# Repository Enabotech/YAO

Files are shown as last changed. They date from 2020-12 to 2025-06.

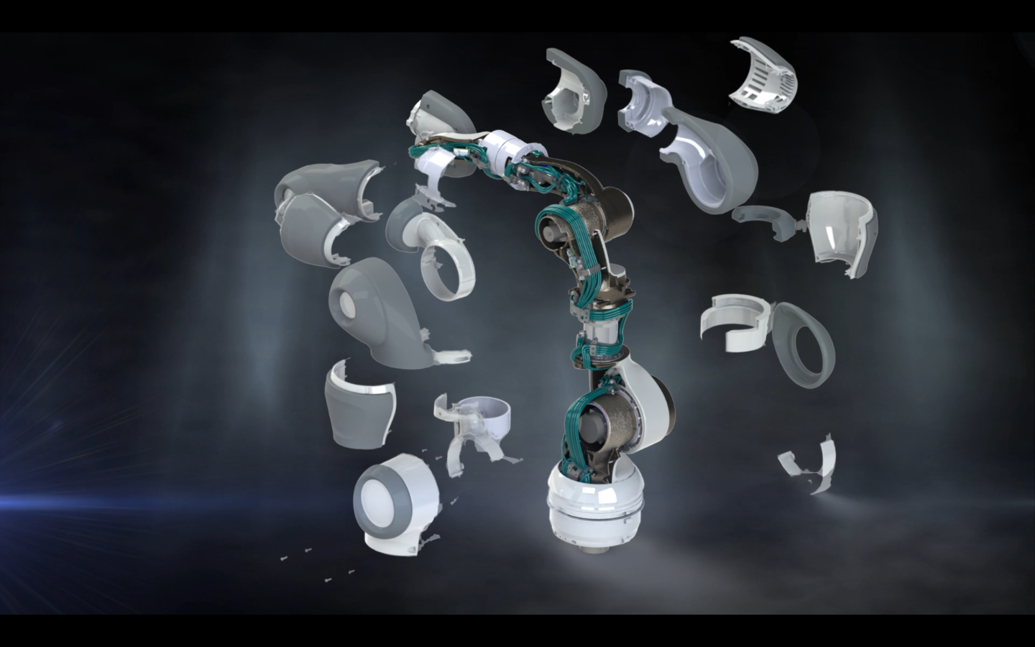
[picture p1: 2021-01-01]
docs/reference/abb/结构图.png

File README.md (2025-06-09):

# YAO
https://github.com/Enabotech/YAO/assets/8104370/9be1e858-5e8b-4420-9542-9bed2b7c62a3

enabotech@126.com

## 电气
### 电机及驱动
* 东方减速步进电机套件。可根据实际需求自行选择合适的电机及驱动方案。
### 运动控制器
* Galil DMC-2183/DMC-4080。可根据实际需求自行选择合适的控制器方案。
### 主控单元
* 基于Ubuntu + ROS Kinetic的PC系统。
## 机械
* 已完成设计及结构验证。主要参考ABB IRB 14000机械臂自行设计。
## 软件
* 完成基于ROS的MOVEIT+GAZEBO仿真系统搭建。
* 初步完成系统框架程序。欢迎PR。
## 逆运动学
| 参数 | 解析解 |
|---|---|
| $\theta_1$ | $$\arctan2(p_y, p_x) - \arcsin{\frac{a_1}{\sqrt{p_x^2 + p_y^2}}}$$ |
| $\theta_2$ | $$\arctan2\left( p_z - d_1, \sqrt{p_x^2 + p_y^2} - a_1 \right) - \arctan2(a_3\sin{\theta_3}, a_2 + a_3\cos{\theta_3})$$ |
| $\theta_3$ | $$\pm \arccos{\frac{L^2 - a_2^2 - a_3^2}{2a_2a_3}}\quad(\text{±号对应肘部"up/down"两种构型})$$ |
| $\theta_4$ | $$\phi - (\theta_2 + \theta_3)$$ |
| $\theta_5$ | $$\arctan2 \left(r_{32}, r_{31}\right)$$ |
| $\theta_6$ | $$\arctan2 \left( \sqrt{r_{11}^2 + r_{21}^2}, r_{33} \right)\quad(\text{为零时退化为万向节锁})$$ |
| $\theta_7$ | $$\arctan2 \left( r_{23}, -r_{13} \right)$$ |
| $\mathbf{p}_{end}$ | $$[p_x, p_y, p_z]^T$$ |
| $L$ | $$\sqrt{(p_z - d_1)^2 + \left( \sqrt{{p_{x}^2 + p_{y}^2}} - a_1 \right)^2}$$ |
| $\phi$ | $$\arg\min \sum_{i=1}^7 \left(\theta_i - \theta_{i,home}\right)^2 \quad (\text{最小能量准则})$$ |
## 图纸
enabot_yao_prj_spec
t
q
w

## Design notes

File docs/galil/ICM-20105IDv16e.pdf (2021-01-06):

ICM-20105ID

## ICM-20105D

ICM-20105D 是为 DMC-21x3 系列运动控制卡配套设计的信号接口板。 ICM-20105D 直 接通过 DIN96 插接在 DMC-21x3 控制卡上，并可通过螺钉锁紧。 ICM-20105D 接口内各引 脚定义与 GALIL 公司的 ICM-20105 基本一致（为方便用户接线与设置， 有个别引脚进行 了调整 ）。

ICM-20105D 上，用户接口为四个运动控制 -反馈接口、一个 I/O 信号接口和一个辅助编 码器接口。

2010 09 | 1 | KIKD

一、运动控制 -反馈接口

DB15 规格的 15 针插座，分别标注为 JX、JY、JZ、JW，对应控制卡上 A（E）、B（F）、 C（G）、D（H）各轴信号。四个接口内的引脚定义是一致的。各引脚信号说明如下：

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
ENABLE+

5V

A-

B-

Z-

V-

SIGN / DIR

9

10

11

12

13

14

15

ENABLE-

GND

A+

B+

Z+

COMMAND

PWM / STEP

V+、V-：
须由用户提供的外部电源，用于驱动电机放大器使能（ SERVER-ON ）信号，四个运动 控制-反馈接口以及辅助编码器接口中的 V+、V-使用同一电源， 用户可以通过任一接口提供 此电源。 V+与 V-之间电压不应大于 30VDC

ENABALE+ 、ENABLE- ：
各轴使能输出信号，用于控制电机放大器或驱动器的使能 （SERVER-ON ）。ENABALE+ 、

ENABLE- 分别为信号隔离光耦的集电极（ Collector ）与发射极（ Emitter ），电流必须由

ENABALE+ 流向 ENABLE- 。
默认状态下， GALIL 控制器使能信号输出为高电平时（电机使能 | SH），ENABALE+ 、
ENABLE- 之间闭合导通； 控制器使能信号输出为低电平时（电机关闭 | MO），ENABALE+ 、

ENABLE- 之间隔离。

默认状态
通过调整 UEN 右侧跳线 X、Y、Z、W 的设置，也可改变上述逻辑状态。 GALIL 控制 器使能信号输出为高电平时 （电机使能 SH），ENABALE+ 、ENABLE- 之间隔离； 控制器使 能信号输出为低电平时（电机关闭 MO），ENABALE+ 、ENABLE- 之间闭合导通。

调整方式，参考板上跳线下的标注。

2010 09 | 2 | KIKD

5V、GND：
DMC-21X3 控制器的 5V 电源，可用于反馈编码器的电源， 也可用于电机运动控制信号 的参考电位。

A+、A-、B+、B-、Z+、Z-：
各轴主编码器反馈信号，直接连至 GALIL 控制器。接收 RS422 或 TTL 信号。

COMMAND ：
各轴+/-10V 电压指令信号，用于控制电机驱动器或放大器。此信号通常用于速度或扭 矩（电流）指令信号。此信号直接连自 GALIL 控制器，以 GND 为参考电位。该信号所能 够提供的电流，请参照 GALIL 控制器手册。

PWM / STEP 、SIGN / DIR ：
各轴的脉冲、方向信号，用于控制电机驱动器或放大器。 此信号通常用于位置指令信号。 此信号直接连自 GALIL 控制器，为 5V TTL 信号。该信号所能够提供的电流， 请参照 GALIL 控制器手册。

用户可以参照附录中的连接举例来按照自己的需求设计此接口与驱动器之间的具体连 接方式，或将驱动器本身的接线说明提供给我们， 由我们协助您实现 ICM-20105D 与您所选 用的驱动器（放大器）的具体连接方式。

二、I/O 信号接口

DB37 规格的 37 孔插座，标注为 JIO，用于连接 I/O 信号。信号与 GALIL 控制卡之间 采用光耦进行了电气隔离。接口中各引脚定义如下：

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
2010 09

INPUT COMMON

INPUT 2

INPUT 4

INPUT 6

INPUT 8

OUTPUT COMMON

OUTPUT 2

OUTPUT 4

OUTPUT 6

3

20 | INPUT 1
21 | INPUT 3
22 | INPUT 5
23 | INPUT 7
24 | ABORT
25 | OUTPUT 1
26 | OUTPUT 3
27 | OUTPUT 5
28 | OUTPUT 7

KIKD

10 | OUTPUT 8
11 | LIMIT SWITCH COMMON
12 | REVERSE LIMIT X
13 | FORWARD LIMIT Y
14 | HOME Y
15 | REVERSE LIMIT Z
16 | FORWARD LIMIT W
17 | HOME W
18 | 5V
19 | GND
29 | READY
30 | FORWARD LIMIT X
31 | HOME X
32 | REVERSE LIMIT Y
33 | FORWARD LIMIT Z
34 | HOME Z
35 | REVERSE LIMIT W
36 | 5V
37 | GND

INPUT COMMON 、INPUT1 —INPUT8 、ABORT：

通用输入以及急停输入信号，对应 GALIL 控制器上的通用输入 IN1（9）、IN2（10）、

IN3（11）、IN3（12）、IN5（13）、IN6（14）、IN7（15）、IN8（16）与急停输入（*1。INPUT COMMOM 为以上信号的内部公共端， 当输入信号引脚与公共端之间有电流时， 为有效输入 （对应 GALIL 控制器输入信号为低）；无电流时，为无效输入，（对应 GALIL 控制器输入信 号为高）。由于使用的光偶器件为双向输入，所以， INPUT COMMOM 既可以接高电平，也 可以接低电平。

ICM-20105ID 输入信号按照 24VDC 规格设计，外部电压 12VDC—30VDC （ 电 流 约 2—6mA）有效。外部电压 0—5VDC（电流小于 1mA）为无效输入。（*2
在 GALIL 的控制器上，通用输入的 1、2、3、4 也可作为位置锁存信号使用。光耦的隔 离处理在增加了应用便利的同时， 也会造成信号相应的延迟，如用户需要比较高的响应速度， 可参照附录中的方式接入位置锁存信号。

OUTPUT COMMON 、OUT1—OUT8、READY ：

通用输出及控制就绪 （异常报警）输出信号，对应 GALIL 控制器的 OUT1（9）、OUT2

（10）、OUT3（11）、OUT4（12）、OUT5（13）、OUT6（14）、OUT7（15）、OUT8（16） 与 ERROR 信号输出。OUTPUT COMMON 为以上输出信号的负公共端。默认状态下，当控 制器输出信号为高电平时， JIO 内相应输出脚与 OUTPUT COMMON 之间导通；当控制器输 出信号为低电平时， JIO 内相应输出脚与 OUTPUT COMMON 之间开路。（*3 输出隔离采用达林顿（ DARLINGTON ）输出光耦元件，开路状态下，最大开路电压为

30V。导通状态下，每路输出信号可通过的最大电流为 | 100mA ，信号输出点与 OUTPUT
2010 09 | 4 | KIKD

COMMON 之间会有约 0.6V 的导通压降，可兼容 TTL 或 HTL 规格。

LIMIT SWITCH COMMON 、FORWARD LIMIT X 、REVERSE LIMIT X 、HOME X 、 FORWARD LIMIT Y 、REVERSE LIMIT Y 、HOME Y、FORWARD LIMIT Z 、REVERSE LIMIT Z、HOME Z 、FORWARD LIMIT W 、REVERSE LIMIT W 、HOME W

各轴的前后极限及原点输入信号， LIMIT SWITCH COMMON 为各轴的前后极限及原点 输入信号的内部公共端， 当输入信号引脚与公共端之间有电流时， 为有效输入（对应 GALIL 控制器输入信号为低）；无电流时，为无效输入，（对应 GALIL 控制器输入信号为高）。由于 使用的光偶器件为双向输入，所以， LIMIT SWITCH COMMOM 既可以接高电平，也可以 接低电平。

ICM-20105ID 输入信号按照 24VDC 规格设计，外部电压 12VDC—30VDC （ 电 流 约 2—6mA）有效。外部电压 0—5VDC（电流小于 1mA）为无效输入。（*2

5V、GND：
GALIL 控制器电源信号，不推荐使用。

三、辅助编码器接口
DB25 规格的 25 孔插座，接口内各引脚定义如下

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
AB- W

AA- W

AB- Z

AA- Z

AB- Y

AA- Y

AB- X

AA- X

NC

5V

V+

COMPARE

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
AB+ W

AA+ W

AB+ Z

AA+ Z

AB+ Y

AA+ Y

AB+ X

AA+ X

NC

GND

V-

AB-W、AB+W、AA-W、AA+W、AB-Z、AB+Z、AA-Z、AA+Z、AB-Y、AB+Y、AA-Y、 AA+Y、AB-X、AB+X、AA-X、AA+X：
各轴的辅助编码器输入信号，也可作为通用输入信号使用（详见《 DMC-21x3 手册》）。 信号直连至 GALIL 运动控制器，可接受 RS422 或 TTL 信号。
2010 09 | 5 | KIKD

5V、GND：
GALIL 控制器电源信号，不推荐使用。

V+、V-：
须由用户提供的外部直流电源，与 JX、JY、JZ、JW 接口中 V+、V-为同一电源，可用 于驱动电机放大器使能（ SERVER-ON ）信号， V+与 V-之间电压不应大于 30VDC

COMPARE ：
位置比较输出信号，直连至 GALIL 运动控制器，为 TTL 输出。
（1.6d 及之前的版本，此引脚未连接。用户如须使用此信号，请参见附录中的说明）

注释：
（*1：默认状态下，急停输入为常开（ normal open ）输入。如用户处于安全考虑，需要采用 常闭（normal close）输入形式，可通过跳线进行调整。该跳线标注为 JPAB。下图为 JPAB 的默认设置状态。
将跳线设置为 | 状态，急停信号为常闭（ normal close）输入。此时，如急
停输入未接线，则 GALIL 控制器不能控制电机运动。

（*2：JIO 接口中，所有输入信号默认状态均为 24VDC 规格，使用 5.6K 阻值的限流电阻。 外部电压 12VDC—30VDC （电流约 2—6mA）为有效输入；外部电压 0—5VDC（电流小 于 1mA）为无效输入。

### 如用户采用较低电压规格的信号，则须在 RPX、RPY、RPZ、RPW、RPIN1A 、RPIN2A

插入 B 型电阻排，通过并联的方式降低信号输入电路中的限流电阻。电阻排的插座在

### ICM-20105ID 的背面。

如输入信号为 TTL 规格，建议采用阻值为 1.0K—1.5K 电阻排；如输入为 12V 规格，建 议采用 10K——15K 阻值的电阻排。

（*3：通用输出与 READY 信号输出的逻辑状态和极性调整
调整 JIO 中的输出信号，涉及到 JPO 跳线以及所有的输出光耦。 JPO 跳线 ICM-20105ID 的左边，JIO 接口下面的位置。光耦元件是接口 JIO 的下方（背面）的双列直插的 IC 元件。 默认状态下， JIO 中的输出信号为为漏型输出（公共端极性为负） ，此时 JPO 下面两针 脚短路，上面针脚悬空； 光耦器件靠右排列， 器件插座左边两个插脚位置悬空（如下图所示 意）。
2010 09 | 6 | KIKD

如特殊情况下， 用户需要采用源型输出 （公共端极性为正），需要将输出光耦元件平移， 靠左排列，使插座右侧的两个位置空闲，同时将 JPO 跳线的上面两个接点短接，下面一个 接脚悬空。

这时，输出电路结构如下图。控制器输出为低电平时， JIO 中相应接点与 OUTPUT

COMMON 导通，OUTPUT COMMON 为正公共端。

2010 09 | 7 | KIKD

附录
1、 RESET 信号的连接
RESET 信号在默认状态下不连接到用户接口中， 如必须使用该信号，可将其接在 JAUX 的 1 或 14 脚。在 JAUX 接口的左下角，预留了 3 个接点的跳线位置（未焊接），左边接点 为 JAUX 的 14 脚（标注为 14），中间接点为 RESERT 信号（标注为 RST），右边接点 JAUX 接口的第 1 脚（标注为 1）。短接相应接点，就可以将 RESET 信号连接到 JAUX 接口的第 1 脚或第 14 脚。RESET 信号本身为 TTL 兼容信号，在接口板上未做任何隔离、保护处理。

2、 位置比较输出信号的连接

在 1.6d 及之前的版本中，位置比较输出信号在默认状态下不连接到输出接口上，如必 须使用该信号，可将其接在 JAUX 的 13 脚。在 JX 与 JY 两个接口之间，略偏上的位置上， 预留了 2 个接点的跳线位置（未焊接），左边接点为 JAUX 的 13 脚（标注为 13），右边接点 为位置比较输出信号 （标注为 CO）。短接这两个接点， 就可以将位置比较输出信号从 JAUX 接口的第 13 脚接出。位置比较输出信号本身为 TTL 信号，在接口板上未做任何隔离、保护 处理。
（在 1.6e 的版本中，取消此跳线，位置比较输出信号已经连接到 JAUX 的 13 脚）

3、 高速位置锁存信号的连接
各轴位置锁存信号与通用输入信号为同一信号。 由于接口板对通用输入信号进行了隔离 处理，会造成一定的信号延迟。 如必须避免这一信号延迟 （例如触发锁存的信号脉冲比较窄， 或确实需要较高的响应速度），可以跨过隔离处理元件，将输入信号从 JAUX 接口直接连到

DMC-21x3 控制器上。
在 JX 与 JY 两个接口之间，略偏上的位置，分别有标注为 14、LX 与 1、LY 的预留跳 线位置（未焊接）。LX 为 X 轴锁存信号（通用输入 1）；LY 为 Y 轴锁存信号（通用输入 2）；

1 为 JAUX 的第 1 脚；14 为 JAUX 的第 14 脚；短接相应接点，就可以将 X、Y 轴的锁存信 号通过 JAUX 接口的第 1 脚、第 14 脚接入。

2010 09 | 8 | KIKD

如果选择了从 JAUX 的 1 脚或 14 脚接入 RESET 信号，则该脚不可同时用于位置锁存 信号的连接。
在 JAUX 接口的右侧， 分别有标注为 LW、10、23、LZ 的预留跳线位置（未焊接）。LW 为 W 轴锁存信号（通用输入 4）；LZ 为 Z 轴锁存信号（通用输入 3）；10 为 JAUX 的第 10 脚；23 为 JAUX 的第 23 脚；短接相应接点，就可以将 Z、W 轴的锁存信号通过 JAUX 接口 的第 10 脚、第 23 脚接入。

4、 版本记录

1.6e

1.6d

1.6c

1.5b

1.4a

1.3a

取消位置比较输出信号跳线，将信号直连至 JAUX 的 13 脚 调整排阻插座的位置，避免空间冲突

调整排阻插座的位置，减少空间冲突
将大部分器件调整到电路板背面，方便用户自行设计控制器外壳 名称由 ICM-20105D 调整为 ICM-20105ID

增加各轴 COMMAND 信号的电压防护电路
将急停设置跳线的标注由 AB 调整为 JPAB

增加 AB 设置跳线
将所有接头外壳通过固定铜柱连接到 GALIL 控制器上。 （DMC-2153 —DMC-2183 的第二接口板下的固定孔本身并未连接至保护地 上，如用户需要，须自行使用导线连接）

最初应用版本
最初试验品

1.2a

1.0a

5、 伺服连接举例
A、 安川 SGDM 系列伺服驱动器的连接

ICM-20105D 连接安川 SGDM 系列伺服驱动器，要为 V+、V- 提供 12—24VDC 电源， 使能设置跳线 X、Y、Z、W 保持默认状态， JX（或 JY、JZ、JW）与驱动器的 CN1 之间如 下表接线：

ICM-20105D — JX
引脚

11

2010 09

SGDM — CN1
引脚

33

信号

A+

9

备注

双绞线

KIKD

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
COMMAND
GND

5V

PWM / STEP

5V

SIGN / DIR

V+

ENABLE+

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
V-REF
SG

PULS+

PULS-

SIGN+

SIGN-

+24VIN

S-ON

位置反馈信号

双绞线
位置反馈信号

双绞线
位置反馈信号

双绞线
速度指令信号

位置指令信号

9、7 ENABALE- 、V-

使能信号
（ICM-20105D 侧 9、7 两引脚短接，不
需要连接至驱动器）

B、松下 MINAS A4 系列伺服驱动器的连接

ICM-20105D 连接松下 MINAS A4 系列伺服驱动器，要为 V+、V- 提供 12—24VDC 电 源，使能设置跳线 X、Y、Z、W 保持默认状态， JX（或 JY、JZ、JW）与驱动器的 CN I/F 之间如下表接线：

ICM-20105D — JX
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
PWM / STEP

5V

SIGN / DIR

COMMAND
GND

V+

ENABLE+

ENABALE- 、
V-

MINAS A4 — CN I/F
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
PULS1

PULS2

SIGN1

SIGN2

SPR
GND

COM+

S-ON

COM-

使能信号
（ICM-20105D 侧 9、7 两引脚短接）

双绞线
速度指令信号

位置指令信号
（MT 参数设置为 2 或 2.5）

备注

双绞线
位置反馈信号

双绞线
位置反馈信号

双绞线
位置反馈信号
2010 09 | 10 | KIKD

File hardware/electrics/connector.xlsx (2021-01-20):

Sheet: vexta signal connector
as signal connector |  |  |  | ar signal connector
Pin | Description | Color | Enabot Wiring | Pin | Description | Color | Enabot Wiring
1 | VCC+5V | brown | 1 | 1
2 | GND | wh-brown | 2 | 2 | GND | wh-brown | 2
3 |  |  |  | 3 | ASG+ | purple | 9
4 | - |  |  | 4 | ASG- | wh-purple | 10
5 | - |  |  | 5 | BSG+ | orange | 7
6 | - |  |  | 6 | BSG- | bl-orange | 8
7 | - |  |  | 7 | TIM1+
8 | - |  |  | 8 | TIM1-
9 | CCW(DIR)+ | green | 3 | 9 | ALARM+ | yellow
10 | CCW(DIR)- | bl-green | 4 | 10 | ALARM- | bl-yellow
11 | CW(PLS)+ | red | 5 | 11 | WNG+
12 | CW(PLS)- | bl-red | 6 | 12 | WNG-
13 |  |  |  | 13 | END+ | gray
14 |  |  |  | 14 | END- | bl-gray
15 |  |  |  | 15 | READY+/AL0+
16 |  |  |  | 16 | READY-/AL0-
17 | BSG2+ | orange | 7 | 17 | TLC+/AL1+
18 | BSG2- | bl-orange | 8 | 18 | TLC‒/AL1‒
19 | ASG2+ | purple | 9 | 19 | TIM2+/AL2+ | blue
20 | ASG2- | wh-purple | 10 | 20 | TIM2-/AL2- | wh-blue
21 | ACL+ | white |  | 21 | GND |  | 2
22 | ACL- | bl-white |  | 22 | IN-COM | brown | 1
23 |  |  |  | 23 | C-ON | black | 12
24 |  |  |  | 24 | CLR/ALM-RST | white
25 | ALARM+ | yellow |  | 25
26 | ALARM- | bl-yellow |  | 26
27 | TIM.2 | blue |  | 27
28 |  |  |  | 28
29 | END+ | gray |  | 29
30 | END- | bl-gray |  | 30
31 | x10 | wh-blue |  | 31 | CW(PLS)+ | red | 5
32 |  |  |  | 32 | CW(PLS)- | bl-red | 6
33 | C.OFF+ | black |  | 33
34 | C.OFF- | wh-black | 12 | 34
35 | - |  |  | 35 | CCW(DIR)+ | green | 3
36 | - |  |  | 36 | CCW(DIR)- | bl-green | 4

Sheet: galil
icm-20105 X/Y/Z axis connector |  |  |  | icm-20105 I/O connector
Pin | Description | Color | Enabot Wiring | Pin | Description | Color | Enabot Wiring
1 | Amp enable common-1/V+ |  | 11 | 1 | Input common
2 | Amp enable |  | 12 | 2 | Input 2
3 | 5 V |  | 1/3/5 | 3 | Input 4
4 | A- |  | 10 | 4 | Input 6
5 | B- |  | 8 | 5 | Input 8
6 | Z- |  |  | 6 | Output supply
7 | NC |  |  | 7 | Output 2
8 | Sign/dir |  | 4 | 8 | Output 4
9 | Amp enable common-2/V- |  |  | 9 | Output 6
10 | Ground |  | 2 | 10 | Output 8
11 | A+ |  | 9 | 11 | Limit switch common | bl-gray | UC
12 | B+ |  | 7 | 12 | Reverse limit X | bl-red | UC
13 | Z+ |  |  | 13 | Forward limit Y | green | UC
14 | Motor command |  |  | 14 | Home Y | gray | UC
15 | PWM/step |  | 6 | 15 | Reverse limit Z | wh-blue | UC
 |  |  |  | 16 | Forward limit W | yellow | UC
 |  |  |  | 17 | Home W | white | UC
 |  |  |  | 18 | 5 V | brown | UC
 |  |  |  | 19 | Ground | black | UC
 |  |  |  | 20 | Input 1
 |  |  |  | 21 | Input 3
 |  |  |  | 22 | Input 5
 |  |  |  | 23 | Input 7
 |  |  |  | 24 | Abort* | wh-black | UC
 |  |  |  | 25 | Output 1
 |  |  |  | 26 | Output 3
 |  |  |  | 27 | Output 5
 |  |  |  | 28 | Output 7
 |  |  |  | 29 | Output return
 |  |  |  | 30 | Forward limit X | red | UC
 |  |  |  | 31 | Home X | purple | UC
 |  |  |  | 32 | Reverse limit Y | bl-green | UC
 |  |  |  | 33 | Forward limit Z | blue | UC
 |  |  |  | 34 | Home Z | orange | UC
 |  |  |  | 35 | Reverse limit W | bl-yellow | UC
 |  |  |  | 36 | 5 V | brown | UC
 |  |  |  | 37 | Ground | black | UC
 |  |  |  |  | *Active low
 |  |  |  |  | UC-Use Color

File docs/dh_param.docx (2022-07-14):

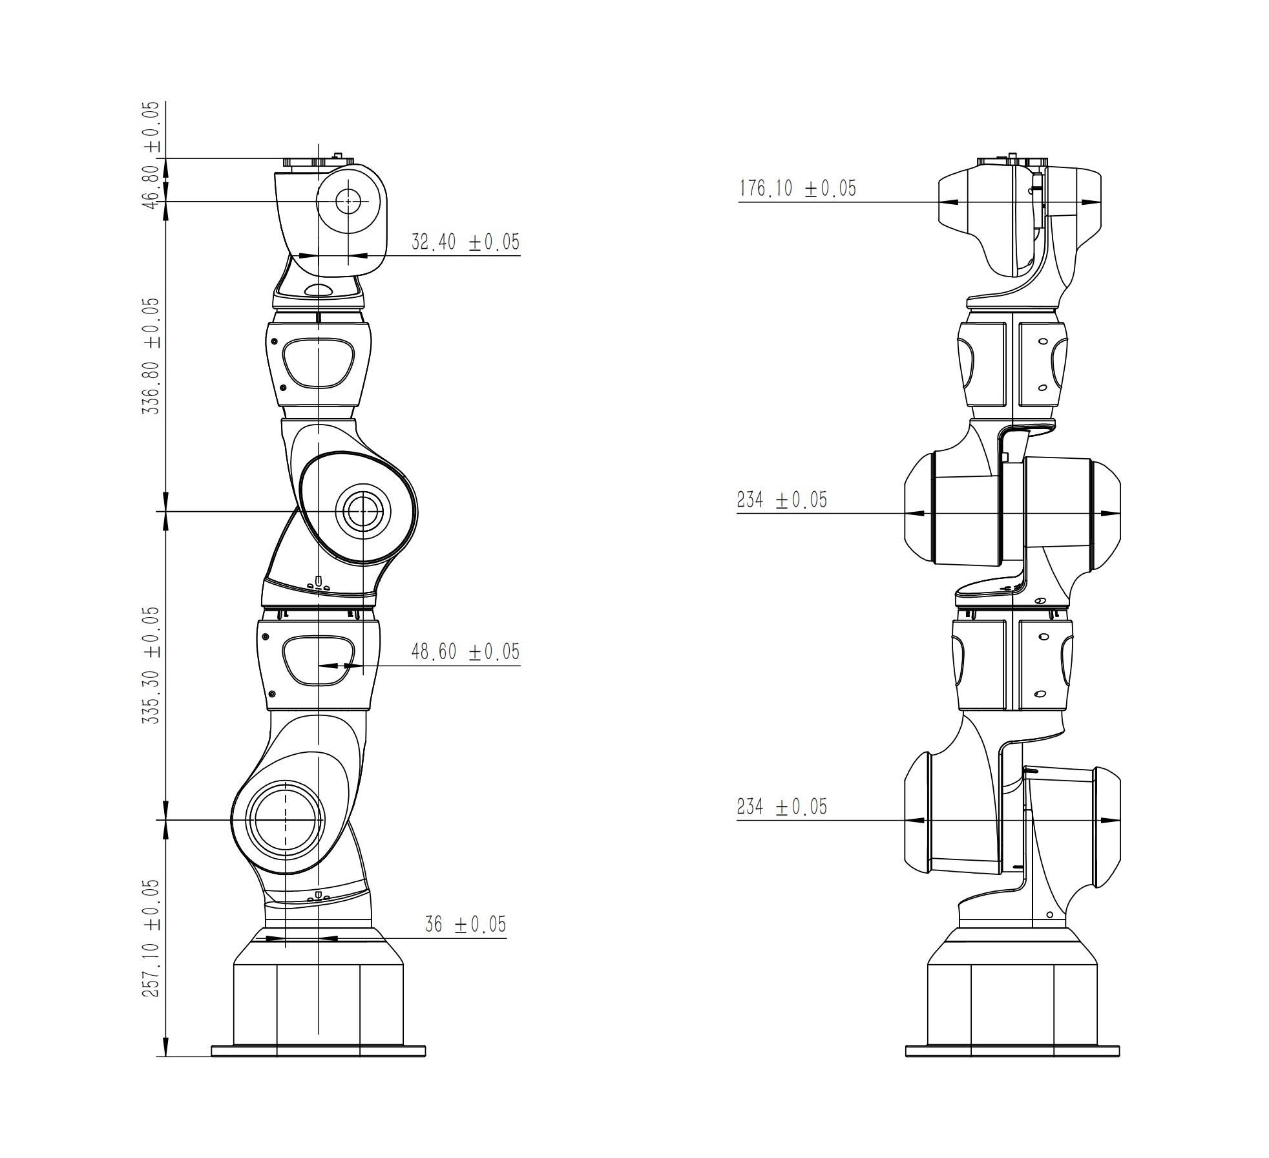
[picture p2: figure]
enabot_yao_prj_spec

SDH | θi | di | ai | αi
1 | θ1 | 257.10 | -36.00 | -90°
2 | θ2 | 0.00 | 36.00 | 90°
3 | θ3 | 335.30 | 48.60 | 90°
4 | θ4 | 0.00 | -48.60 | -90°
5 | θ5 | 336.80 | 32.40 | -90°
6 | θ6 | 0.00 | -32.40 | 90°
7 | θ7 | 46.80 | 0.00 | 0°
MDH | αi-1 | ai-1 | θi | di
1 | 0° | 0.00 | 180°+θ1 | 257.10
2 | 90° | 36.00 | 180°+θ2 | 0
3 | 90° | 36.00 | θ3 | 335.30
4 | 90° | 48.60 | 180°+θ4 | 0
5 | 90° | 48.60 | θ5 | 336.80
6 | 90° | -32.40 | 180°+θ6 | 0
7 | 90° | -32.40 | θ7 | 46.80

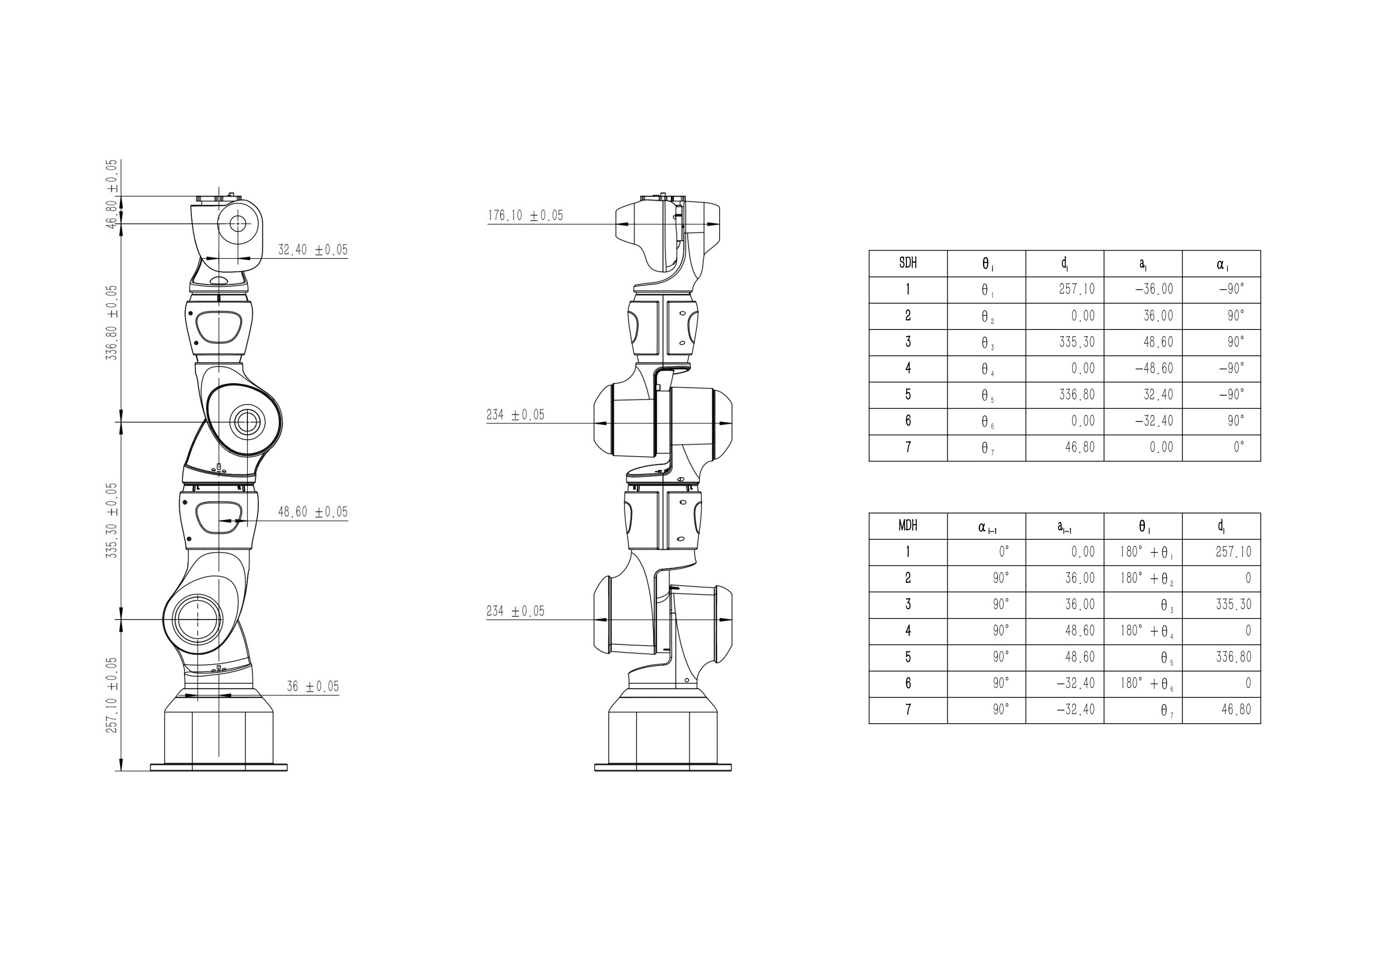
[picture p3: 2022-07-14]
docs/enabot_yao_prj_spec.jpg

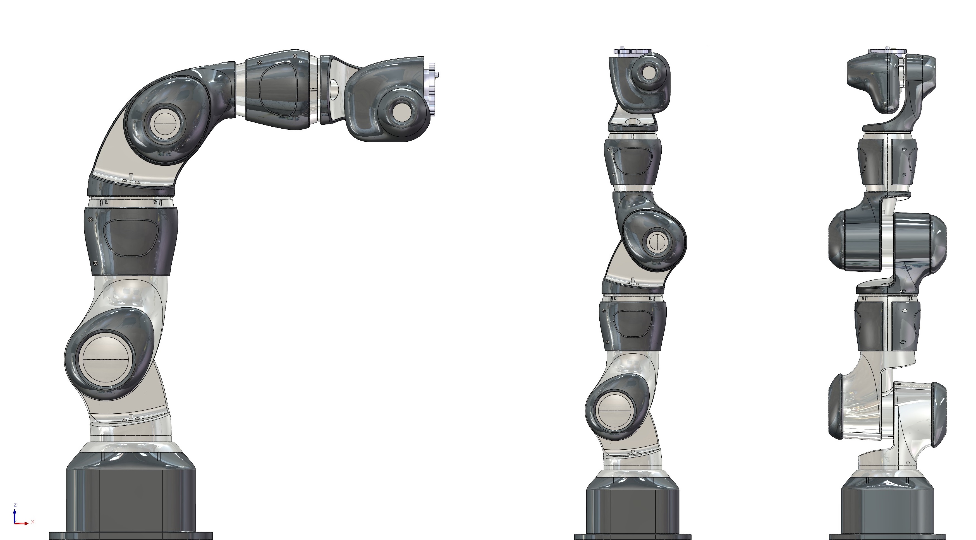
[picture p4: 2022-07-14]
docs/enabot_yao_views.jpg

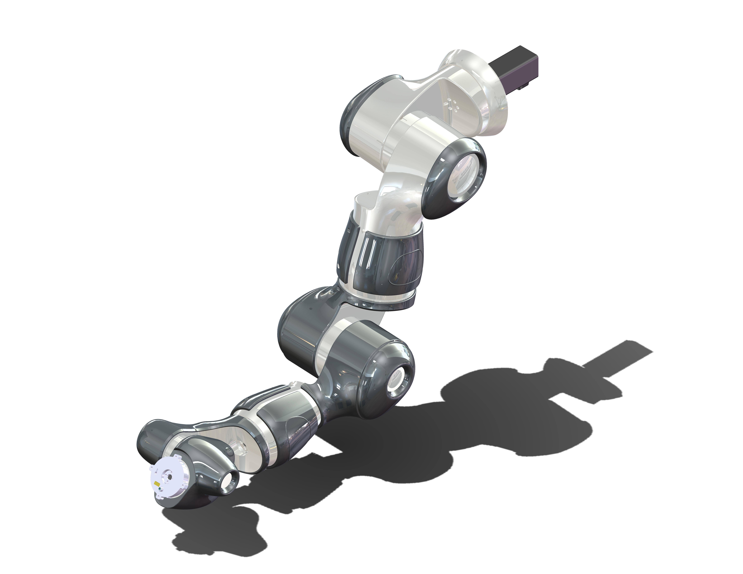
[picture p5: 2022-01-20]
docs/enabot_arm_r_perspect_b_800.JPG

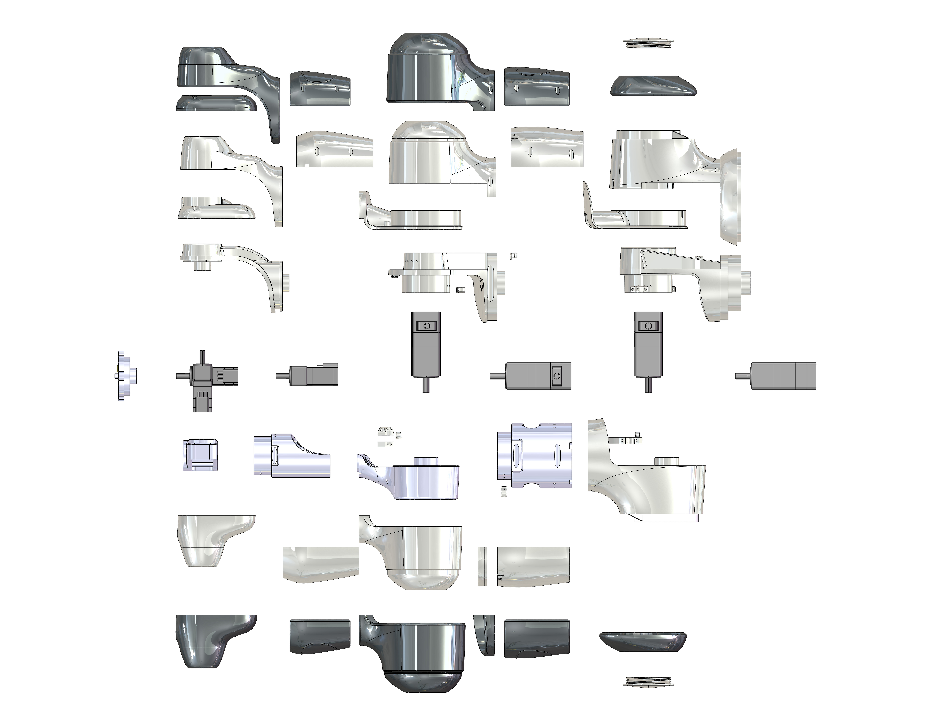
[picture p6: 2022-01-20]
docs/enabot_arm_r_bomb_top_800.JPG

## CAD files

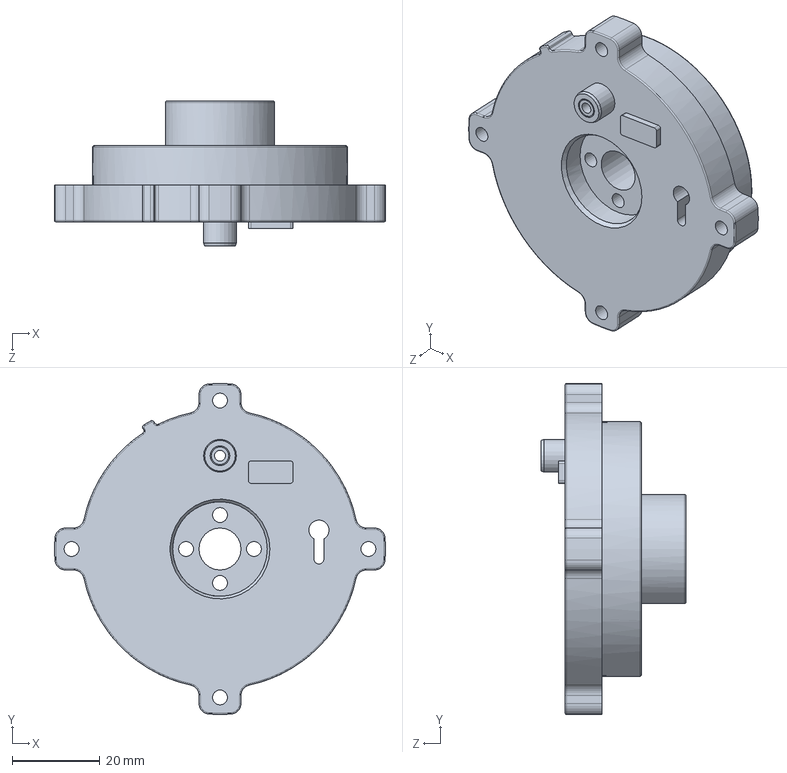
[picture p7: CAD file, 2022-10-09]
mechanism/manufacture/l7r.SLDASM
75.6 x 75.6 x 33.1 mm

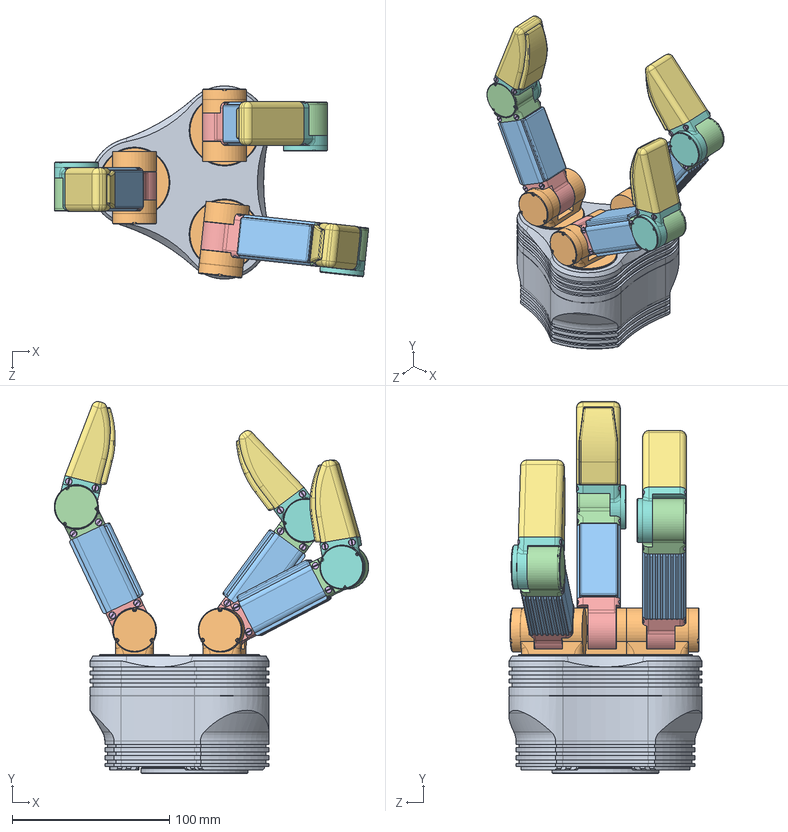
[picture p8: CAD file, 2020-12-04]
mechanism/model/finger/Schunk SDH-2.sldasm
199.8 x 236.3 x 122.7 mm
Baza
PodnoePrsta x 3
FingerMid-2 x 3
FingerMid-3 x 3
FingerMid-1 x 3
slotted cheese head screw_din_ISO 1207 - M2.5 x 3 --- 3N x 36
FingerTip-2 x 3
FingerTip-1 x 3

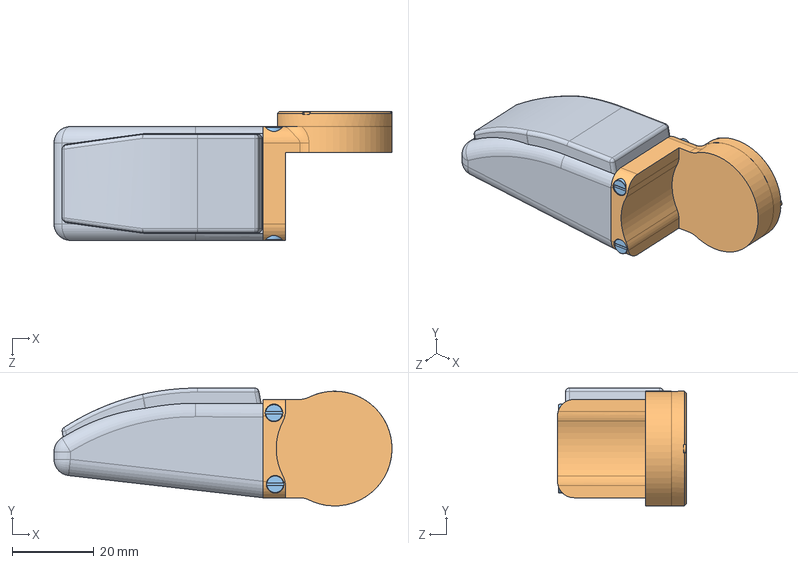
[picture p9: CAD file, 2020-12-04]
mechanism/model/finger/FingerTip.sldasm
82.5 x 28.8 x 31.4 mm
FingerTip-2
FingerTip-1
slotted cheese head screw_din_ISO 1207 - M2.5 x 3 --- 3N x 4

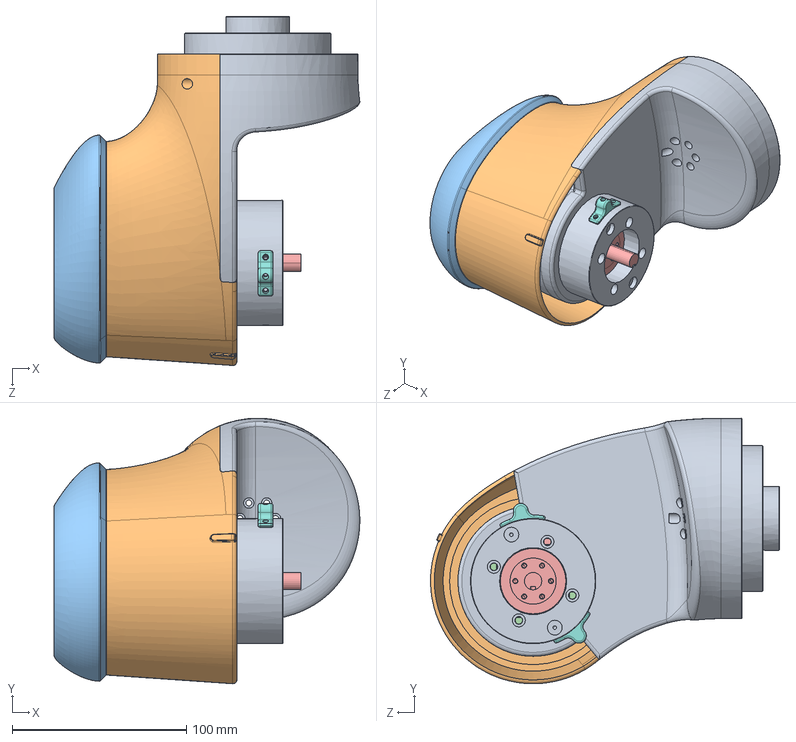
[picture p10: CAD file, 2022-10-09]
mechanism/manufacture/l1r.SLDASM
175.7 x 152.6 x 200.6 mm
l1r主轴
l1r主壳
l1r轴2侧大盖
l1r轴2侧小盖
B308-A
l1r线缆支架a
l1r线缆支架b
机械制动1-a x 2

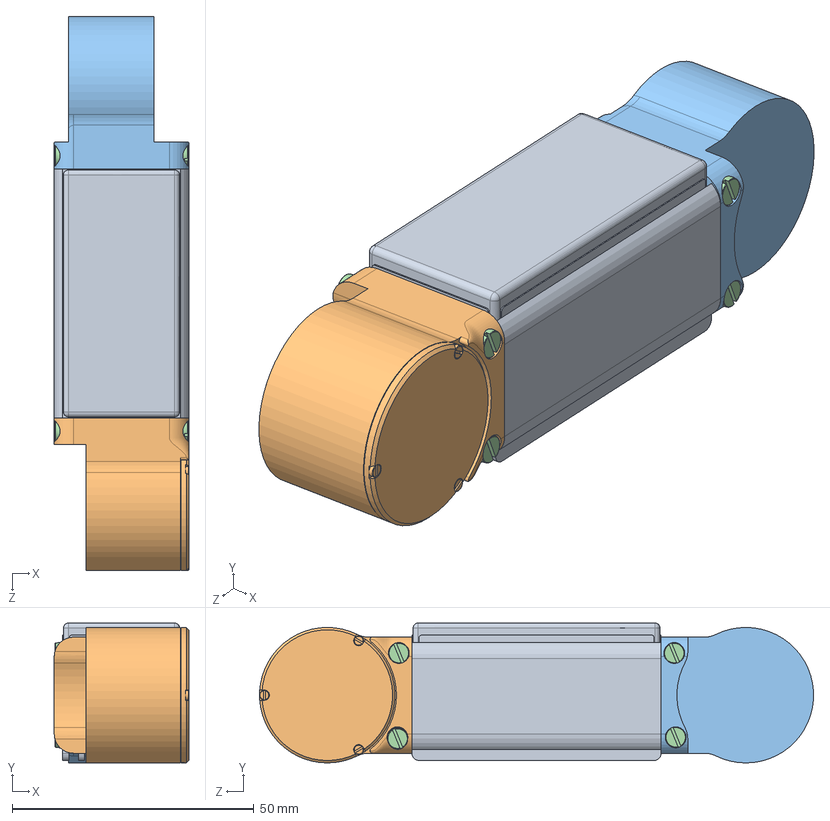
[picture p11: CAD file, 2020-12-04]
mechanism/model/finger/FingerMid.sldasm
27.8 x 28.9 x 114.5 mm
FingerMid-2
FingerMid-3
FingerMid-1
slotted cheese head screw_din_ISO 1207 - M2.5 x 3 --- 3N x 8

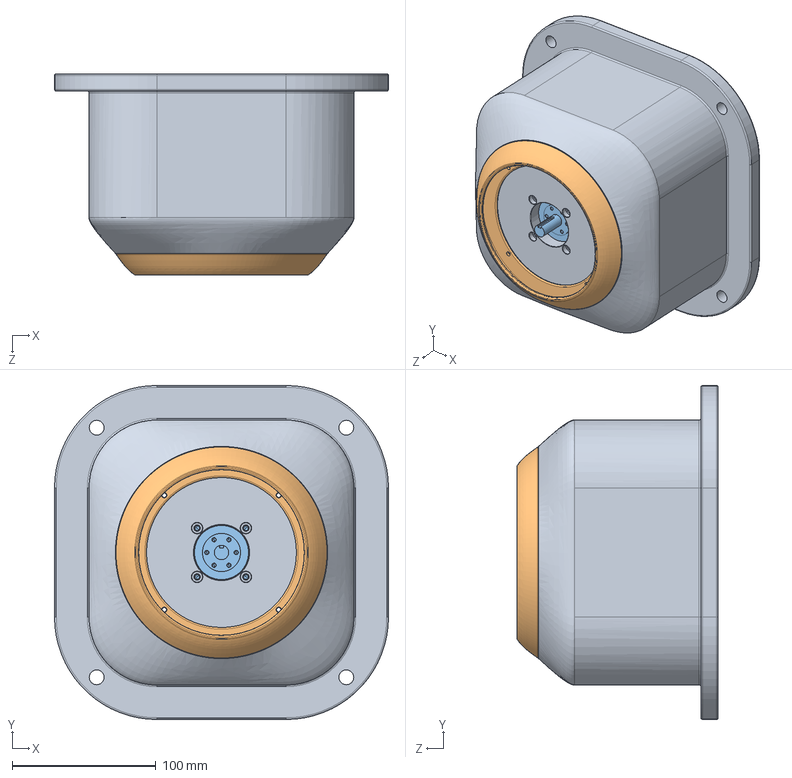
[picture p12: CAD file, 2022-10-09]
mechanism/manufacture/lbb.SLDASM
232.2 x 232.2 x 140.0 mm
lbb基座
lbb轴1外壳
B308-A

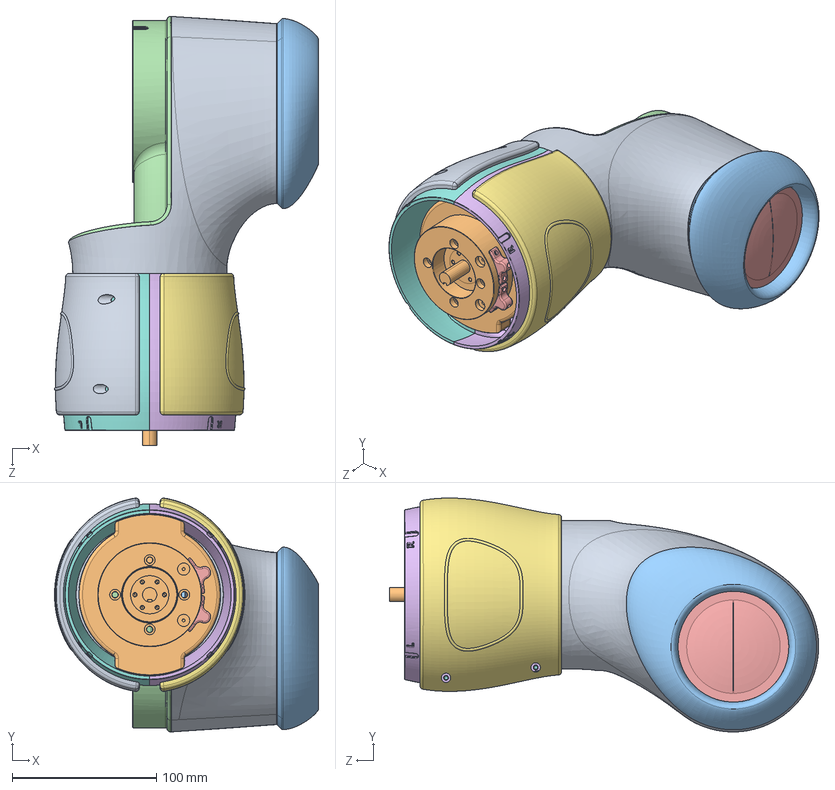
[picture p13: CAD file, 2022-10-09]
mechanism/manufacture/l2r.SLDASM
183.0 x 162.1 x 297.6 mm
l2r主轴b
l2r主轴c
l2r轴2侧大盖
l2r轴2侧壳
l2r轴2侧小盖
l2r轴7右内壳
l2r轴7右外壳
l2r轴7左内壳
l2r轴7左外壳
B308-A
l2r线缆支架a
l2r线缆支架b
机械制动1-a x 2
机械制动1-b

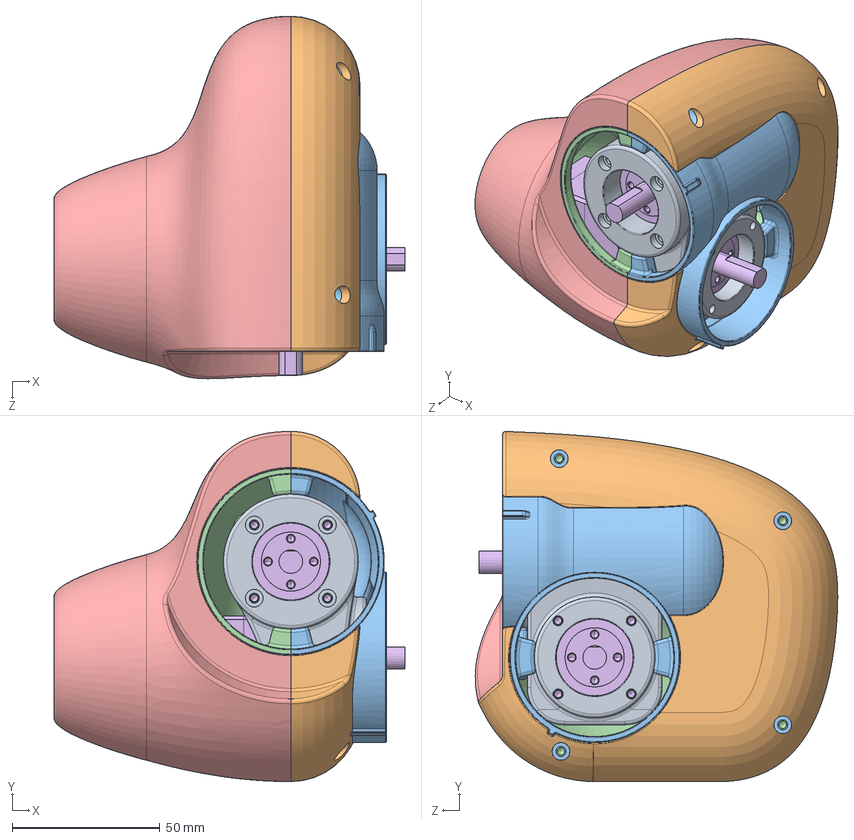
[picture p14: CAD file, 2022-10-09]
mechanism/manufacture/l6r.SLDASM
118.7 x 118.4 x 122.6 mm
l6r主轴
l6r右外壳
l6r右内壳
l6r左内壳
l6r左外壳
B710-A x 2

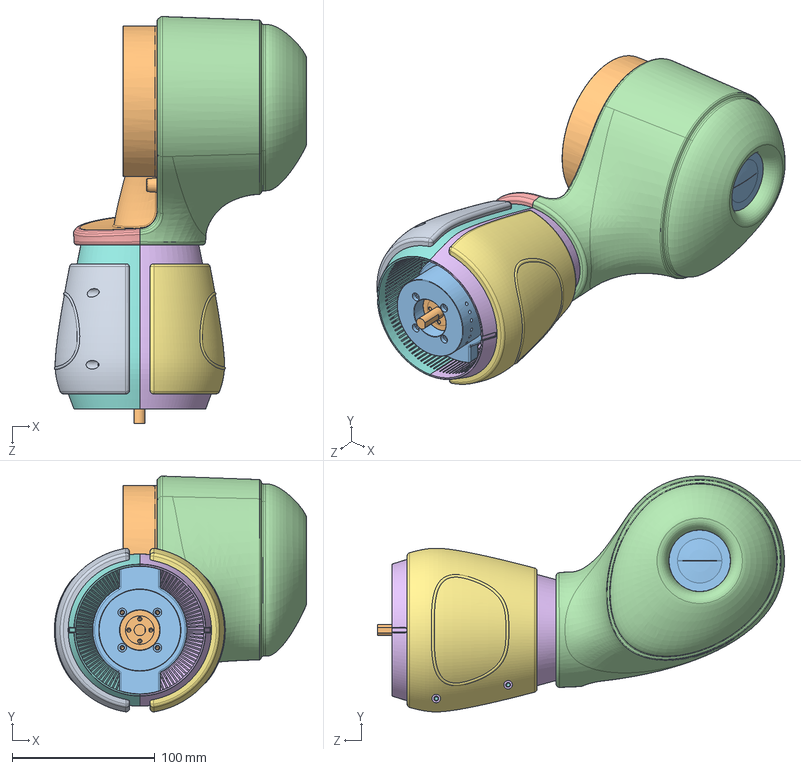
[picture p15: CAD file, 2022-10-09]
mechanism/manufacture/l4r.SLDASM
177.0 x 165.4 x 285.5 mm
l4r主轴
l4r轴3内侧壳
l4r轴3内壳
l4r轴3外壳a
l4r轴3外壳b
l4r轴4右内壳
l4r轴4右外壳
l4r轴4左内壳
l4r轴4左外壳
B710-A
l4r主轴b
l4r线缆支架a
l4r线缆支架b
机械制动1-b

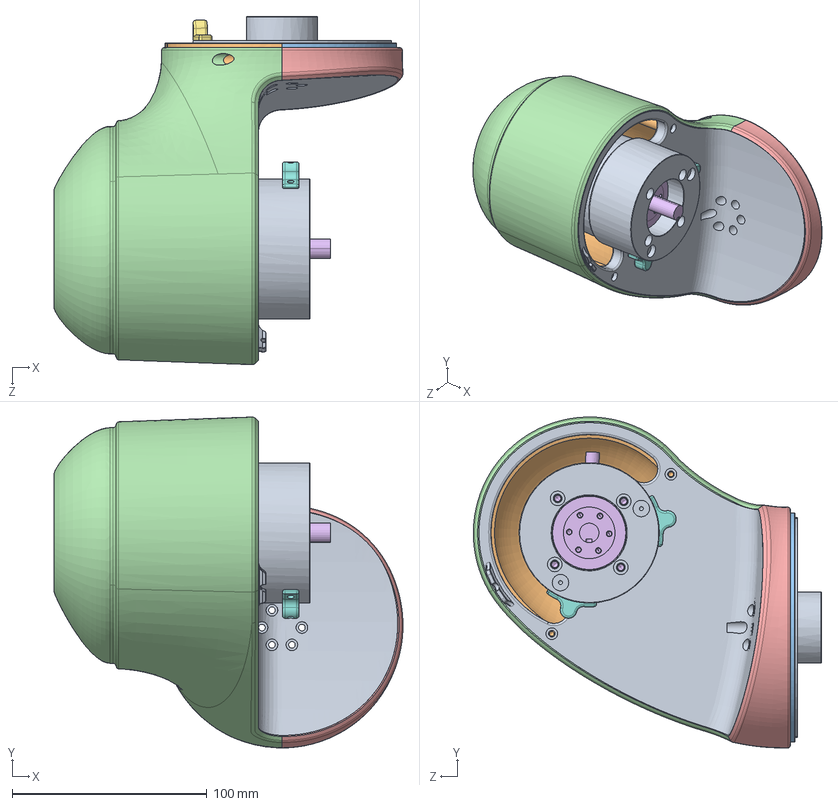
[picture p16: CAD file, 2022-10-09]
mechanism/manufacture/l3r.SLDASM
179.1 x 169.8 x 178.8 mm
l3r主轴
l3r轴3内壳a
l3r轴3内壳b
l3r轴3外壳a
l3r轴3外壳b
B308-A
机械制动1-b
机械制动1-a x 2

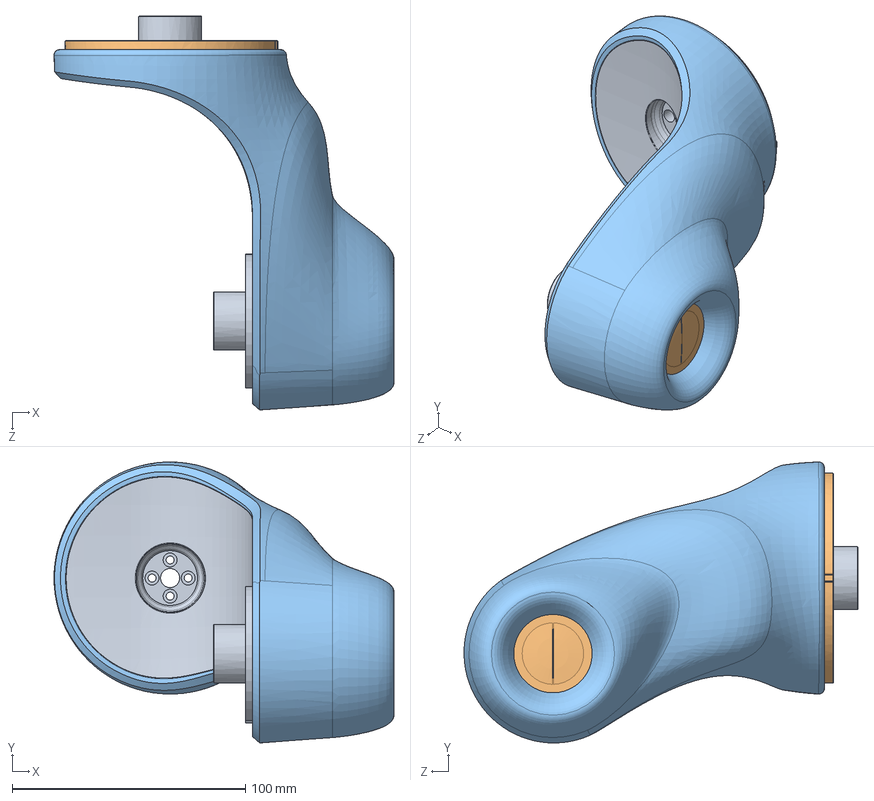
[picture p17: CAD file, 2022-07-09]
mechanism/manufacture/l5r.SLDASM
145.8 x 120.5 x 168.9 mm
l5r主轴
l5r右内壳
l5r右外壳

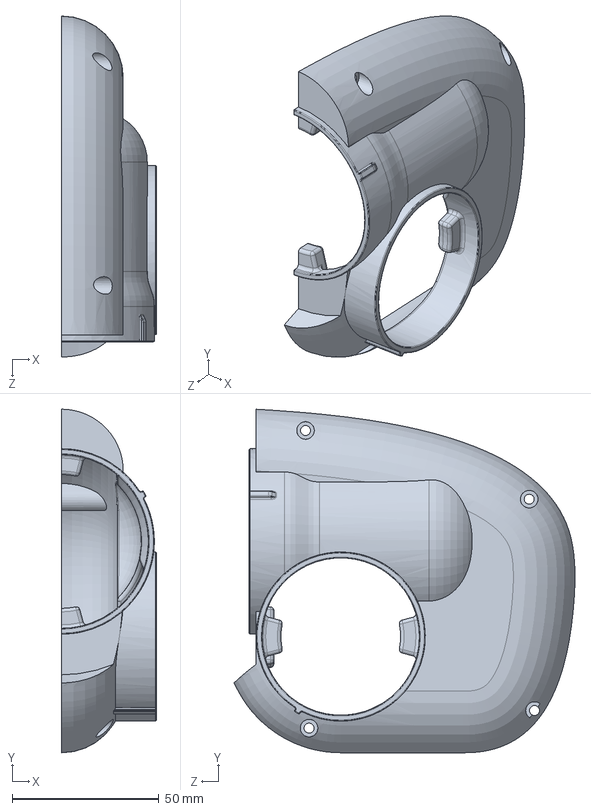
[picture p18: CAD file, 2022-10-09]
mechanism/manufacture/l6r右内壳.sldprt
32.3 x 117.1 x 116.2 mm

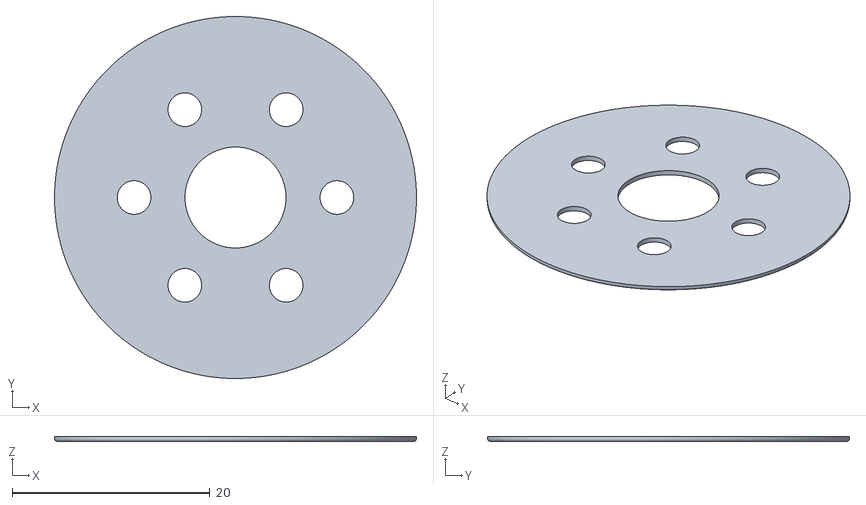
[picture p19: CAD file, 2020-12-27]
mechanism/manufacture/stl/主轴垫片-0.5mm.STL
36.6 x 36.6 x 0.5

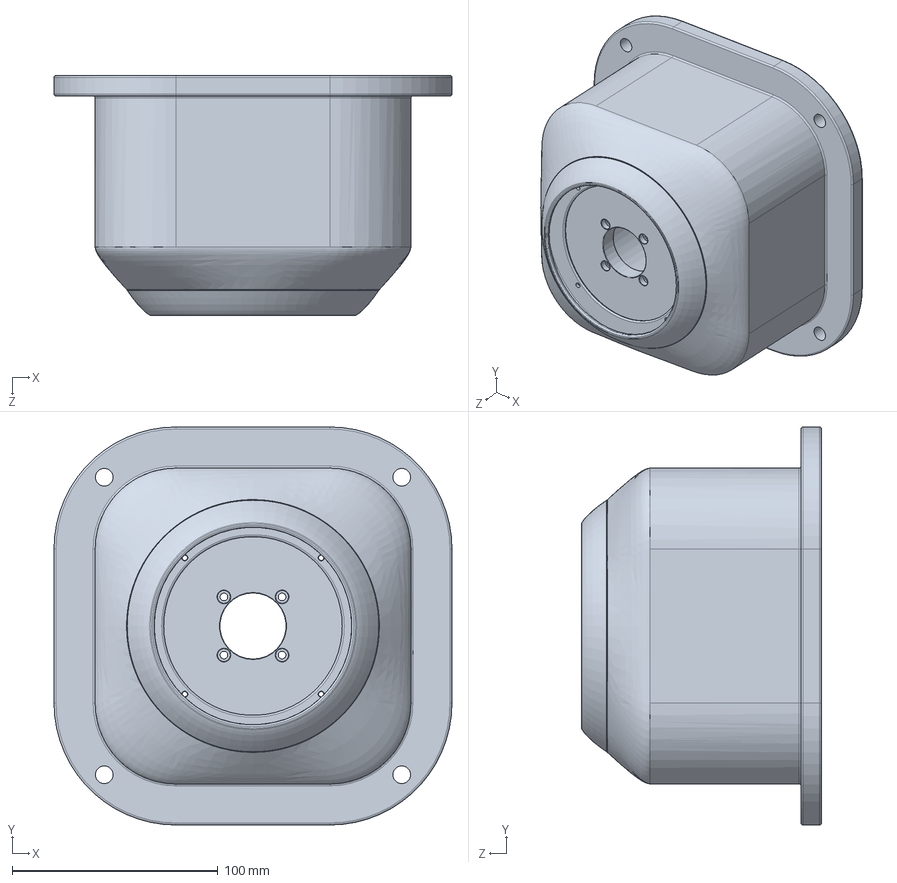
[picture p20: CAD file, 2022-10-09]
mechanism/model/arm/base/lbb.SLDPRT
193.5 x 193.5 x 116.7 mm

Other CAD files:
mechanism/model/finger/FRANG_.sldasm
mechanism/model/arm/l7r/l7r.SLDPRT
mechanism/model/finger/FingerTip-2.sldprt
mechanism/model/sim/enabot_v5/lbb.SLDPRT
mechanism/manufacture/B308-A.SLDPRT
mechanism/manufacture/B710-A.SLDPRT
mechanism/manufacture/l1r主壳.sldprt
mechanism/manufacture/l1r主轴.sldprt
mechanism/manufacture/l1r主轴垫片.sldprt
mechanism/manufacture/l1r电机安装垫片.SLDPRT
mechanism/manufacture/l1r线缆支架a.SLDPRT
mechanism/manufacture/l1r线缆支架b.sldprt
mechanism/manufacture/l1r轴2侧大盖.sldprt
mechanism/manufacture/l1r轴2侧小盖.sldprt
mechanism/manufacture/l2r主轴b.sldprt
mechanism/manufacture/l2r主轴c.sldprt
mechanism/manufacture/l2r线缆支架a.sldprt
mechanism/manufacture/l2r线缆支架b.sldprt
mechanism/manufacture/l2r轴2侧壳.sldprt
mechanism/manufacture/l2r轴2侧大盖.sldprt
mechanism/manufacture/l2r轴2侧小盖.sldprt
mechanism/manufacture/l2r轴7右内壳.sldprt
mechanism/manufacture/l2r轴7右外壳.sldprt
mechanism/manufacture/l2r轴7左内壳.sldprt
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

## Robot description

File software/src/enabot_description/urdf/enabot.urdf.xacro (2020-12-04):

<?xml version="1.0"?>
<robot name="enabot" xmlns:xacro="http://www.ros.org/wiki/xacro">
  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
  <xacro:include filename="$(find enabot_description)/urdf/materials.xacro" />
  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
  <xacro:include filename="$(find enabot_description)/urdf/enabot.gazebo.xacro" />
  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
  <xacro:include filename="$(find enabot_description)/urdf/enabot.transmission.xacro" />
  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
  <xacro:include filename="$(find enabot_description)/urdf/utilities.xacro" />
  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
  <xacro:include filename="$(find enabot_description)/urdf/enabot_servo_gripper.xacro"/>
  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
  <xacro:include filename="$(find enabot_description)/gazebo/gazebo.urdf.xacro"/>

  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
  <xacro:property name="joint_damping" value="0.5" />
  <xacro:property name="max_effort" value="300"/>



  <xacro:macro name="enabot" params="parent name hardware_interface">

    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
    <joint name="${parent}_joint" type="fixed">
      <origin xyz="0 0 0" rpy="0 0 0"/>
      <parent link="${parent}"/>
      <child link="${name}_base"/>
    </joint>

    <link name="${name}_base">
      <inertial>
        <origin xyz="0 0 0" rpy="0 0 0"/>
        <mass value="15"/>
        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
      </inertial>

      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

    </link>


   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
    <joint name="${name}_joint_1_r" type="revolute">
      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
      <parent link="${name}_base"/>
      <child link="${name}_link_1_r"/>
      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
      <origin xyz="0 -0.25626 0.565" rpy="${PI / 2} ${PI / 6} 0"/>
      <axis xyz="0 0 1"/>
      <limit lower="${-168.5 * PI / 180}" upper="${168.5 * PI / 180}" effort="${max_effort}" velocity="${180 * PI / 180}" />
      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
      <dynamics damping="${joint_damping}"/>
    </joint>

   <link name="${name}_link_1_r">
      <inertial>
        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
        <origin xyz="0 0 0" rpy="0 0 0"/>
        <mass value="2"/>
        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
      </inertial>

      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
    </link>

   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
    <joint name="${name}_joint_2_r" type="revolute">
      <parent link="${name}_link_1_r"/>
      <child link="${name}_link_2_r"/>
      <origin xyz="0.03 0.0 0.1" rpy="${PI / 2} ${PI / 2} 0.0"/>
      <axis xyz="0 0 1"/>
      <limit lower="${-143.5 * PI / 180}" upper="${43.5 * PI / 180}" effort="${max_effort}" velocity="${180 * PI / 180}" />
      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
      <dynamics damping="${joint_damping}"/>
    </joint>

   <link name="${name}_link_2_r">
      <inertial>
        <origin xyz="0 0 0" rpy="0 0 0"/>
        <mass value="2"/>
        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
      </inertial>

      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
    </link>

   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
    <joint name="${name}_joint_7_r" type="revolute">
      <parent link="${name}_link_2_r"/>
      <child link="${name}_link_3_r"/>
      <origin xyz="-0.03 0.17283 0.0" rpy="${-PI / 2} ${-PI} 0.0"/>
      <axis xyz="0 0 1"/>
      <limit lower="${-168.5 * PI / 180}" upper="${168.5 * PI / 180}" effort="${max_effort}" velocity="${180 * PI / 180}" />
      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
      <dynamics damping="${joint_damping}"/>
    </joint>

   <link name="${name}_link_3_r">
      <inertial>
        <origin xyz="0 0 0" rpy="0 0 0"/>
        <mass value="2"/>
        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
      </inertial>

      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
    </link>

   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
    <joint name="${name}_joint_3_r" type="revolute">
      <parent link="${name}_link_3_r"/>
      <child link="${name}_link_4_r"/>
      <origin xyz="-0.04188 0.0 0.07873" rpy="${PI / 2} ${- PI / 3} 0.0"/>
      <axis xyz="0 0 1"/>
      <limit lower="${-123.5 * PI / 180}" upper="${80 * PI / 180}" effort="${max_effort}" velocity="${180 * PI / 180}" />
      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
      <dynamics damping="${joint_damping}"/>
    </joint>

   <link name="${name}_link_4_r">
      <inertial>
        <origin xyz="0 0 0" rpy="0 0 0"/>
        <mass value="2"/>
        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
      </inertial>

      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
    </link>

   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
    <joint name="${name}_joint_4_r" type="revolute">
      <parent link="${name}_link_4_r"/>
      <child link="${name}_link_5_r"/>
      <origin xyz="0.0405 0.16461 0.0" rpy="-${PI / 2} 0.0 0.0"/>
      <axis xyz="0 0 1"/>
      <limit lower="${-290 * PI / 180}" upper="${290 * PI / 180}" effort="${max_effort}" velocity="${400 * PI / 180}" />
      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
      <dynamics damping="${joint_damping}"/>
    </joint>

   <link name="${name}_link_5_r">
      <inertial>
        <origin xyz="0 0 0" rpy="0 0 0"/>
        <mass value="2"/>
        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
      </inertial>

      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
    </link>

   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
    <joint name="${name}_joint_5_r" type="revolute">
      <parent link="${name}_link_5_r"/>
      <child link="${name}_link_6_r"/>
      <origin xyz="-0.027 0 0.10039" rpy="${PI / 2} 0.0 0.0"/>
      <axis xyz="0 0 1"/>
      <limit lower="${-88 * PI / 180}" upper="${138 * PI / 180}" effort="${max_effort}" velocity="${400 * PI / 180}" />
      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
      <dynamics damping="${joint_damping}"/>
    </joint>

   <link name="${name}_link_6_r">
      <inertial>
        <origin xyz="0 0 0" rpy="0 0 0"/>
        <mass value="2"/>
        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
      </inertial>

      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
    </link>

   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
    <joint name="${name}_joint_6_r" type="revolute">
      <parent link="${name}_link_6_r"/>
      <child link="${name}_link_7_r"/>
      <origin xyz="0.027 0.029 0.0" rpy="-${PI / 2} 0.0 0.0"/>
      <axis xyz="0 0 1"/>
      <limit lower="${-229 * PI / 180}" upper="${229 * PI / 180}" effort="${max_effort}" velocity="${400 * PI / 180}" />
      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
      <dynamics damping="${joint_damping}"/>
    </joint>

   <link name="${name}_link_7_r">
      <inertial>
        <origin xyz="0 0 0" rpy="0 0 0"/>
        <mass value="2"/>
        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
      </inertial>

      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
    </link>


    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
    <xacro:enabot_gazebo name="${name}" />
    <xacro:enabot_transmission name="${name}" hardware_interface="${hardware_interface}"/>

  </xacro:macro>




  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
  <link name="world"/>

  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
  <xacro:enabot name="enabot" hardware_interface="PositionJointInterface" parent="world">


  </xacro:enabot>

  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

</robot>

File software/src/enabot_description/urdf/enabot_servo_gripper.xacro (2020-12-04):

<?xml version="1.0"?>
<robot name="enabot" xmlns:xacro="http://www.ros.org/wiki/xacro">

  <!-- Import all Gazebo-customization elements, including Gazebo colors -->
  <xacro:include filename="$(find enabot_description)/urdf/enabot_servo_gripper.gazebo.xacro" />
  <!-- Import Transmissions -->
  <xacro:include filename="$(find enabot_description)/urdf/enabot_servo_gripper.transmission.xacro" />
  <!-- Include Utilities -->
  <xacro:include filename="$(find enabot_description)/urdf/utilities.xacro" />

  <!-- some constants -->
 <!-- <xacro:property name="safety_controller_k_pos" value="100" />
  <xacro:property name="safety_controller_k_vel" value="2" /> -->
  <xacro:property name="joint_damping" value="0.5" />
  <xacro:property name="max_effort" value="300"/>
 
  <xacro:macro name="enabot_servo_gripper" params="parent name hardware_interface *origin">

    <!--joint between {parent} and base-->
    <joint name="${parent}_joint" type="fixed">
      <xacro:insert_block name="origin"/>
      <parent link="${parent}"/>
      <child link="${name}_base"/>
    </joint>

    <link name="${name}_base">
      <inertial>
        <origin xyz="0 0 0" rpy="0 0 0"/>
        <mass value="0.2"/>
        <inertia ixx="0.0001" ixy="0" ixz="0" iyy="0.0001" iyz="0" izz="0.0001" />
      </inertial>

      <visual>
        <origin xyz="0 0 0" rpy="0 0 0"/>
        <geometry>
          <mesh filename="package://enabot_description/meshes/gripper/base.stl"/>
        </geometry>
        <material name="Light_Grey"/>
      </visual>

      <collision>
        <origin xyz="0 0 0" rpy="0 0 0"/>
        <geometry>
          <mesh filename="package://enabot_description/meshes/gripper/coarse/base.stl"/>
        </geometry>
        <material name="Light_Grey"/>
      </collision>

    </link>

    <!-- joint between base and right finger -->
    <joint name="${name}_joint" type="prismatic">
      <parent link="${name}_base"/>
      <child link="${name}_finger_r"/>
      <origin xyz="0 -0.0065 0.0837" rpy="0 0 0"/>
      <axis xyz="-1 0 0"/>
      <limit lower="0" upper="0.025" effort="${max_effort}" velocity="0.02" />
      <!--   <safety_controller soft_lower_limit="${-168 * M_PI / 180}" soft_upper_limit="${168 * M_PI / 180}" k_position="${safety_controller_k_pos}" k_velocity="${safety_controller_k_vel}"/> -->
      <dynamics damping="${joint_damping}"/>
    </joint>

    <link name="${name}_finger_r">
      <inertial>
        <origin xyz="0 0 0" rpy="0 0 0"/>
        <mass value="0.01"/>
        <inertia ixx="0.000001" ixy="0" ixz="0" iyy="0.000001" iyz="0" izz="0.000001" />
      </inertial>

      <visual>
        <origin xyz="0 0 0" rpy="0 0 0"/>
        <geometry>
          <mesh filename="package://enabot_description/meshes/gripper/finger.stl"/>
        </geometry>
        <material name="Grey"/>
      </visual>

      <collision>
        <origin xyz="0 0 0" rpy="0 0 0"/>
        <geometry>
          <mesh filename="package://enabot_description/meshes/gripper/coarse/finger.stl"/>
        </geometry>
        <material name="Grey"/>
      </collision>
    </link>

   <!-- joint between base and left finger -->
    <joint name="${name}_joint_m" type="prismatic">
      <parent link="${name}_base"/>
      <child link="${name}_finger_l"/>
      <origin xyz="0 0.0065 0.0837" rpy="0 0 ${PI}"/>
      <axis xyz="-1 0 0"/>
      <limit lower="0" upper="0.025" effort="${max_effort}" velocity="0.02" />
      <!--   <safety_controller soft_lower_limit="${-168 * M_PI / 180}" soft_upper_limit="${168 * M_PI / 180}" k_position="${safety_controller_k_pos}" k_velocity="${safety_controller_k_vel}"/> -->
      <dynamics damping="${joint_damping}"/>
      <mimic joint="${name}_joint"/>
    </joint>

    <link name="${name}_finger_l">
      <inertial>
        <origin xyz="0 0 0" rpy="0 0 0"/>
        <mass value="0.01"/>
        <inertia ixx="0.000001" ixy="0" ixz="0" iyy="0.000001" iyz="0" izz="0.000001" />
      </inertial>

      <visual>
        <origin xyz="0 0 0" rpy="0 0 0"/>
        <geometry>
          <mesh filename="package://enabot_description/meshes/gripper/finger.stl"/>
        </geometry>
        <material name="Grey"/>
      </visual>

      <collision>
        <origin xyz="0 0 0" rpy="0 0 0"/>
        <geometry>
          <mesh filename="package://enabot_description/meshes/gripper/coarse/finger.stl"/>
        </geometry>
        <material name="Grey"/>
      </collision>
    </link>

     <!--Extensions -->
    <xacro:enabot_servo_gripper_gazebo name="${name}" />
    <xacro:enabot_servo_gripper_transmission name="${name}" hardware_interface="${hardware_interface}"/>

  </xacro:macro>

</robot>

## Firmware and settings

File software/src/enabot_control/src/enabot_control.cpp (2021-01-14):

#include <enabot_control.h>
#include <galil_dmc_4060.h>
#include <list>

//#include "armplaning_client.h"


using namespace std;

#ifdef __RIGHT_ARM__
typedef actionlib::SimpleActionServer<control_msgs::FollowJointTrajectoryAction> R_TrajectoryServer;
std::list<robotState> r_targetPointList;		// list of points to move to
#endif //__RIGHT_ARM__

#ifdef __LEFT_ARM__
typedef actionlib::SimpleActionServer<control_msgs::FollowJointTrajectoryAction> L_TrajectoryServer;
std::list<robotState> l_targetPointList;		// list of points to move to
#endif //__LEFT_ARM__

double deg2rad = (3.1415926535897931/180.0);
double rad2deg = (180.0/3.1415926535897931);
 


GCon g = 0;

#ifdef __RIGHT_ARM__
//***************************************************************************
// Processing and JointTrajectoryAction
void r_executeTrajectory(const control_msgs::FollowJointTrajectoryGoalConstPtr& r_goal, R_TrajectoryServer* r_as)
{
  robotState rs;

  float lastDuration = 0.0;


  int nrOfPoints = r_goal->trajectory.points.size();		// Number of points to add
  for(int i=0; i<nrOfPoints; i++)
  {
	  // ros values come in rad, internally we work in degree
	  rs.j[0] = r_goal->trajectory.points[i].positions[0]*rad2deg;	//j1
	  rs.j[1] = r_goal->trajectory.points[i].positions[1]*rad2deg;	//j2
	  rs.j[2] = r_goal->trajectory.points[i].positions[2]*rad2deg;	//j3
	  rs.j[3] = r_goal->trajectory.points[i].positions[3]*rad2deg;	//j4
	  rs.j[4] = r_goal->trajectory.points[i].positions[4]*rad2deg;	//j5
	  rs.j[5] = r_goal->trajectory.points[i].positions[5]*rad2deg;	//j6
	  rs.j[6] = r_goal->trajectory.points[i].positions[6]*rad2deg;	//j7

	  float dtmp = r_goal->trajectory.points[i].time_from_start.toSec();
	  rs.duration = dtmp - lastDuration;// time_from_start is adding up, these values are only for the single motion
	  lastDuration = dtmp;

	  r_targetPointList.push_back(rs);//push_back() 在list的末尾添加一个元素 

      ROS_INFO("right arm recv position: %d, %d, %d, %d, %d, %d, %d, duration: %f", \
			(int)(r_goal->trajectory.points[i].positions[0]*rad2deg*ANGLE2PULSE), \
			(int)(r_goal->trajectory.points[i].positions[1]*rad2deg*ANGLE2PULSE), \
			(int)(r_goal->trajectory.points[i].positions[2]*rad2deg*ANGLE2PULSE), \
			(int)(r_goal->trajectory.points[i].positions[3]*rad2deg*ANGLE2PULSE), \
			(int)(r_goal->trajectory.points[i].positions[4]*rad2deg*ANGLE2PULSE), \
			(int)(r_goal->trajectory.points[i].positions[5]*rad2deg*ANGLE2PULSE), \
			(int)(r_goal->trajectory.points[i].positions[6]*rad2deg*ANGLE2PULSE), \
			r_goal->trajectory.points[i].time_from_start.toSec());

      ROS_INFO("right arm recv velocity: %d, %d, %d, %d, %d, %d, %d, duration: %f", \
			(int)(r_goal->trajectory.points[i].velocities[0]*rad2deg*ANGLE2PULSE), \
			(int)(r_goal->trajectory.points[i].velocities[1]*rad2deg*ANGLE2PULSE), \
			(int)(r_goal->trajectory.points[i].velocities[2]*rad2deg*ANGLE2PULSE), \
			(int)(r_goal->trajectory.points[i].velocities[3]*rad2deg*ANGLE2PULSE), \
			(int)(r_goal->trajectory.points[i].velocities[4]*rad2deg*ANGLE2PULSE), \
			(int)(r_goal->trajectory.points[i].velocities[5]*rad2deg*ANGLE2PULSE), \
			(int)(r_goal->trajectory.points[i].velocities[6]*rad2deg*ANGLE2PULSE), \
			r_goal->trajectory.points[i].time_from_start.toSec());
  }

  r_as->setSucceeded();

  //debug msg
 ROS_INFO("final right arm recv position: %f %f %f %f %f %f %f,duration: %f", rs.j[0],rs.j[1],rs.j[2],rs.j[3],rs.j[4],rs.j[5],rs.j[6],rs.duration);

}
#endif //__RIGHT_ARM__


#ifdef __LEFT_ARM__
//***************************************************************************
// Processing and JointTrajectoryAction
void l_executeTrajectory(const control_msgs::FollowJointTrajectoryGoalConstPtr& l_goal, R_TrajectoryServer* l_as)
{
  //double rad2deg = 180.0 / 3.141;

 robotState ls;

 float lastDuration = 0.0;

  int nrOfPoints = l_goal->trajectory.points.size();		// Number of points to add
  for(int i=0; i<nrOfPoints; i++){
	  ls.j[0] = l_goal->trajectory.points[i].positions[0]*rad2deg;	// ros values come in rad, internally we work in degree
	  ls.j[1] = l_goal->trajectory.points[i].positions[1]*rad2deg;
	  ls.j[2] = l_goal->trajectory.points[i].positions[2]*rad2deg;
	  ls.j[3] = l_goal->trajectory.points[i].positions[3]*rad2deg;
	  ls.j[4] = l_goal->trajectory.points[i].positions[4]*rad2deg;
	  ls.j[5] = l_goal->trajectory.points[i].positions[5]*rad2deg;
	  ls.j[6] = l_goal->trajectory.points[i].positions[6]*rad2deg;
	  
	  float dtmp = l_goal->trajectory.points[i].time_from_start.toSec();
	  ls.duration = dtmp - lastDuration;// time_from_start is adding up, these values are only for the single motion
	  lastDuration = dtmp;

	  l_targetPointList.push_back(ls);//push_back() 在list的末尾添加一个元素 
  }
  l_as->setSucceeded();

  //debug msg
 ROS_INFO("left arm recv: %f %f %f %f %f %f %f,duration: %f", ls.j[0],ls.j[1],ls.j[2],ls.j[3],ls.j[4],ls.j[5],ls.j[6],ls.duration);
}
#endif //__LEFT_ARM__

//*************************************************************************
void quit(int sig)
{
  ros::shutdown();
  exit(0);
}

//******************** MAIN ************************************************
int main(int argc, char** argv)
{
	ros::init(argc, argv, "enabot_mover");
	ros::NodeHandle r_nh, l_nh;


	ROS_INFO("...connect to galil motion controller... return conde is [%d]",  MotorControllerInit(&g));

#ifdef __RIGHT_ARM__
	//Start the ActionServer for JointTrajectoryActions and GripperCommandActions from MoveIT
	R_TrajectoryServer r_tserver(r_nh, "enabot_mover_r/follow_joint_trajectory", boost::bind(&r_executeTrajectory, _1, &r_tserver), false);
  	ROS_INFO("TrajectoryActionServer: Starting");
  	r_tserver.start();
#endif //__RIGHT_ARM__

#ifdef __LEFT_ARM__
	L_TrajectoryServer l_tserver(l_nh, "enabot_mover_l/follow_joint_trajectory", boost::bind(&l_executeTrajectory, _1, &l_tserver), false);
  	ROS_INFO("TrajectoryActionServer: Starting");
  	l_tserver.start();
#endif //__LEFT_ARM__

	// Start the robot
	dual_arm_robot::enabot_control robot;
	robot.init();	
	robot.mainLoop();		//spinning is done inside the main loop			

  	signal(SIGINT,quit);	
	return(0);
}

namespace dual_arm_robot
{
	//*************************************************************************************

	enabot_control::~enabot_control(){

	}
	//*************************************************************************************
	void enabot_control::init(){
		ROS_INFO("...initing...");

		flag_stop_requested = false;
		//this deside the control msg send frequency 
		cycleTime = 20.0;// in ms
		JointsNum = MAX_JOINT_NUM;

#ifdef __RIGHT_ARM__
		r_setPointState.j[0] =  0.0;	// initialized values to be usable for rob right arm 
		r_setPointState.j[1] =  0.0;
		r_setPointState.j[2] =  0.0;
		r_setPointState.j[3] =  0.0;
		r_setPointState.j[4] =  0.0;
		r_setPointState.j[5] =  0.0;
		r_setPointState.j[6] =  0.0;
		r_setPointState.duration = 0;
#endif //__RIGHT_ARM__

#ifdef __LEFT_ARM__
		l_setPointState.j[0] =  0.0;	// initialized values to be usable for rob left arm 
		l_setPointState.j[1] =  0.0;
		l_setPointState.j[2] =  0.0;
		l_setPointState.j[3] =  0.0;
		l_setPointState.j[4] =  0.0;
		l_setPointState.j[5] =  0.0;
		l_setPointState.j[6] =  0.0;
		l_setPointState.duration = 0;
#endif //__LEFT_ARM__

		// when starting up (or when reading the HW joint values) the target position has to be aligned with the setPoint position
		for(int i=0; i<JointsNum; i++)
		{
#ifdef __RIGHT_ARM__
			r_targetState.j[i] = r_setPointState.j[i];
#endif //__RIGHT_ARM__

#ifdef __LEFT_ARM__
			l_targetState.j[i] = l_setPointState.j[i];
#endif //__LEFT_ARM__
		}
			
#ifdef __RIGHT_ARM__
        	r_targetState.duration = 0.0;	//init the timeStamp
#endif //__RIGHT_ARM__

#ifdef __LEFT_ARM__
		l_targetState.duration = 0.0;	//init the timeStamp
#endif //__LEFT_ARM__

		for(int j=0; j<=JointsNum; j++)
		{
#ifdef __RIGHT_ARM__
			r_controlData[j] = 0;
#endif //__RIGHT_ARM__

#ifdef __LEFT_ARM__
			l_controlData[j] = 0;
#endif //__LEFT_ARM__
		}

#ifdef __RIGHT_ARM__
		r_msgJointsCurrent.header.stamp = ros::Time::now();
		r_msgJointsCurrent.name.resize(MAX_JOINT_NUM);
		r_msgJointsCurrent.position.resize(MAX_JOINT_NUM);
		r_msgJointsCurrent.name[0] ="enabot_joint_1_r";
		r_msgJointsCurrent.position[0] = 0.0;
		r_msgJointsCurrent.name[1] ="enabot_joint_2_r";
		r_msgJointsCurrent.position[1] = 0.0;
		r_msgJointsCurrent.name[2] ="enabot_joint_3_r";
		r_msgJointsCurrent.position[2] = 0.0;
		r_msgJointsCurrent.name[3] ="enabot_joint_4_r";
		r_msgJointsCurrent.position[3] = 0.0;
		r_msgJointsCurrent.name[4] ="enabot_joint_5_r";
		r_msgJointsCurrent.position[4] = 0.0;
		r_msgJointsCurrent.name[5] ="enabot_joint_6_r";
		r_msgJointsCurrent.position[5] = 0.0;
		r_msgJointsCurrent.name[6] ="enabot_joint_7_r";
		r_msgJointsCurrent.position[6] = 0.0;
#endif //__RIGHT_ARM__

#ifdef __LEFT_ARM__
		l_msgJointsCurrent.header.stamp = ros::Time::now();
		l_msgJointsCurrent.name.resize(MAX_JOINT_NUM);
		l_msgJointsCurrent.position.resize(MAX_JOINT_NUM);
		l_msgJointsCurrent.name[0] ="enabot_joint_1_l";
		l_msgJointsCurrent.position[0] = 0.0;
		l_msgJointsCurrent.name[1] ="enabot_joint_2_l";
		l_msgJointsCurrent.position[1] = 0.0;
		l_msgJointsCurrent.name[2] ="enabot_joint_3_l";
		l_msgJointsCurrent.position[2] = 0.0;
		l_msgJointsCurrent.name[3] ="enabot_joint_4_l";
		l_msgJointsCurrent.position[3] = 0.0;
		l_msgJointsCurrent.name[4] ="enabot_joint_5_l";
		l_msgJointsCurrent.position[4] = 0.0;
		l_msgJointsCurrent.name[5] ="enabot_joint_6_l";
		l_msgJointsCurrent.position[5] = 0.0;
		l_msgJointsCurrent.name[6] ="enabot_joint_7_l";
		l_msgJointsCurrent.position[6] = 0.0;
#endif //__LEFT_ARM__

		// Publish the current joint states
		pubJoints = nh.advertise<sensor_msgs::JointState>("/joint_states", 1);

	}

	//*************************************************************************************
	void enabot_control::mainLoop()
	{
  		ROS_INFO("Starting Mover Main Loop");
		
		//output angle data to a txt file
		int i = 0;
  		
 	 	for(;;)
  		{
			MotionGeneration();			// Generate the joint motion 
			CommunicationHW();			// Forward the new setpoints to the hardware

			if(flag_stop_requested)
				break;

			ros::spinOnce();

  			//ros::MultiThreadedSpinner s(2);  //多线程
  			//ros::spin(s);  

			ros::Duration(cycleTime/1000.0).sleep();		// main loop with 20 Hz.(50/1000=0.05s=50ms)
  		}

		ROS_INFO("Closing Mover Main Loop");

		if (g) x_e(GClose(g)); 
		{
			g = 0; //close g
			ROS_INFO("...dmc controller closed...");
		}
	} 
	//************************************************************************************
	//
	void enabot_control::MotionGeneration()
	{
		int i=0;
		int j=0;

		//printf("r_targetPointList.size() = %ld \n",r_targetPointList.size());
       
#ifdef __RIGHT_ARM__
		if(r_targetPointList.size() > 0)
		{
			r_targetState = r_targetPointList.front();
			r_targetPointList.pop_front();

			for(int i=0; i<JointsNum; i++)
			{
				r_setPointState.j[i] = r_targetState.j[i];
			}
			r_setPointState.duration = r_targetState.duration;
			
			for(j=0;j<JointsNum;j++)
			{
				r_controlData[j] = r_setPointState.j[j];
			}
			r_controlData[MAX_JOINT_NUM] = r_setPointState.duration;
		}

#endif

#ifdef __LEFT_ARM__
		if(l_targetPointList.size() > 0)
		{

			l_targetState = l_targetPointList.front();
			l_targetPointList.pop_front();

			for(int i=0; i<JointsNum; i++)
			{
				l_setPointState.j[i] = l_targetState.j[i];
			}
			l_setPointState.duration = l_targetState.duration;
			
			for(j=0;j<JointsNum;j++)
			{
				l_controlData[j] = l_setPointState.j[j];
			}
			l_controlData[MAX_JOINT_NUM] = l_setPointState.duration;
		}
#endif
	}
	//************************************************************************************
	// Forward the new setpoints to the hardware

	void enabot_control::CommunicationHW()
	{

		int i = 0;
		for(i=0; i<=JointsNum; i++)//write right arm control data
		{
#ifdef __RIGHT_ARM__
			r_executeData[i] = r_controlData[i];
#endif

#ifdef __LEFT_ARM__
			l_executeData[i] = l_controlData[i];
#endif
		}

#ifdef __RIGHT_ARM__
		if(r_executeData[0]!=r_executeData_old[0] && r_executeData[1]!=r_executeData_old[1])
		{
			
			//add send mesage command here	
			//************************************
			ROS_INFO("motor testing ... angle: [%f][%f][%f][%f][%f][%f][%f] ... return code: [%d]", \
			r_executeData[0], r_executeData[1], r_executeData[2], r_executeData[3], r_executeData[4], r_executeData[5], r_executeData[6], \
			MotorTest(&g, r_executeData));



			Comm.SetRightJoints(r_executeData);//send new target angle 
			ROS_INFO("Right arm MSG [%f][%f][%f][%f][%f][%f][%f][%f]", r_executeData[0],r_executeData[1],r_executeData[2],r_executeData[3],r_executeData[4],r_executeData[5],r_executeData[6],r_executeData[7]);

			//save the date to old
			for (int i=0;i<=JointsNum;i++)
			{
				r_executeData_old[i] = r_executeData[i];
			}



			R_CommunicationROS();			// Publish the joint states and error info
		}
#endif

#ifdef __LEFT_ARM__
		if(l_executeData[0]!=l_executeData_old[0] && l_executeData[1]!=l_executeData_old[1])
		{
			//add send mesage command here		
			//************************************

			Comm.SetLeftJoints(l_executeData);//send new target angle 

			//************************************


			ROS_INFO("Left arm MSG [%f][%f][%f][%f][%f][%f][%f][%f]", l_executeData[0],l_executeData[1],l_executeData[2],l_executeData[3],l_executeData[4],l_executeData[5],l_executeData[6],l_executeData[7]);

			//save the date to old
			for (int i=0;i<=JointsNum;i++)
			{
				l_executeData_old[i] = l_executeData[i];
			}

			L_CommunicationROS();			// Publish the joint states and error info
		}
#endif
	}

#ifdef __RIGHT_ARM__
	//************************************************************************************
	// forward the current joints to RViz etc
	void enabot_control::R_CommunicationROS()
	{
		r_msgJointsCurrent.header.stamp = ros::Time::now();
		r_msgJointsCurrent.position[0] = r_executeData[0]*deg2rad;		// Robot SER communication works in degree
		r_msgJointsCurrent.position[1] = r_executeData[1]*deg2rad;
		r_msgJointsCurrent.position[2] = r_executeData[2]*deg2rad;
		r_msgJointsCurrent.position[3] = r_executeData[3]*deg2rad;
		r_msgJointsCurrent.position[4] = r_executeData[4]*deg2rad;
		r_msgJointsCurrent.position[5] = r_executeData[5]*deg2rad;
		r_msgJointsCurrent.position[6] = r_executeData[6]*deg2rad;


/*		int Position[8], Velocity[8], Torque[8];
		GetMotorState(&g,Position,Velocity,Torque);

		ROS_INFO("...[%d][%d][%d][%d][%d][%d][%d]...\n", 		Position[0], \
															Position[1], \
															Position[2], \
															Position[3], \
															Position[4], \
															Position[5], \
															Position[6]);


		r_msgJointsCurrent.position[0] = Position[0]*PULSE2ANGLE*deg2rad;
		r_msgJointsCurrent.position[1] = Position[1]*PULSE2ANGLE*deg2rad;
		r_msgJointsCurrent.position[2] = Position[2]*PULSE2ANGLE*deg2rad;
		r_msgJointsCurrent.position[3] = Position[3]*PULSE2ANGLE*deg2rad;
		r_msgJointsCurrent.position[4] = Position[4]*PULSE2ANGLE*deg2rad;
		r_msgJointsCurrent.position[5] = Position[5]*PULSE2ANGLE*deg2rad;
		r_msgJointsCurrent.position[6] = r_executeData[6]*deg2rad;

		ROS_INFO("...[%f][%f][%f][%f][%f][%f][%f]...\n", 	r_msgJointsCurrent.position[0], \
															r_msgJointsCurrent.position[1], \
															r_msgJointsCurrent.position[2], \
															r_msgJointsCurrent.position[3], \
															r_msgJointsCurrent.position[4], \
															r_msgJointsCurrent.position[5], \
															r_msgJointsCurrent.position[6]);
*/

		pubJoints.publish(r_msgJointsCurrent);	// ROS communication works in Radian
	}
#endif

#ifdef __LEFT_ARM__
	//************************************************************************************
	// forward the current joints to RViz etc
	void enabot_control::L_CommunicationROS()
	{
		l_msgJointsCurrent.header.stamp = ros::Time::now();
		l_msgJointsCurrent.position[0] = l_executeData[0]*deg2rad;		// Robot SER communication works in degree
		l_msgJointsCurrent.position[1] = l_executeData[1]*deg2rad;
		l_msgJointsCurrent.position[2] = l_executeData[2]*deg2rad;
		l_msgJointsCurrent.position[3] = l_executeData[3]*deg2rad;
		l_msgJointsCurrent.position[4] = l_executeData[4]*deg2rad;
		l_msgJointsCurrent.position[5] = l_executeData[5]*deg2rad;
		l_msgJointsCurrent.position[6] = l_executeData[6]*deg2rad;

		pubJoints.publish(l_msgJointsCurrent);	// ROS communication works in Radian

	}
#endif

}

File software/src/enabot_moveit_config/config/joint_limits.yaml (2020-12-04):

# joint_limits.yaml allows the dynamics properties specified in the URDF to be overwritten or augmented as needed    
# Specific joint properties can be changed with the keys [max_position, min_position, max_velocity, max_acceleration]
# Joint limits can be turned off with [has_velocity_limits, has_acceleration_limits]
joint_limits:
  enabot_joint_1_r:
    has_position_limits: true
    min_position: -2.94087978961
    max_position:  2.94087978961
    has_velocity_limits: true
    max_velocity: 3.14159265359 
    has_acceleration_limits: false
    max_acceleration: 0
  enabot_joint_2_r:
    has_position_limits: true
    min_position: -2.50454747661
    max_position:  0.75921822462
    has_velocity_limits: true
    max_velocity: 3.14159265359 
    has_acceleration_limits: false
    max_acceleration: 0
  enabot_joint_3_r:
    has_position_limits: true
    min_position: -2.15548162621
    max_position:  1.39626340160
    has_velocity_limits: true
    max_velocity: 3.14159265359 
    has_acceleration_limits: false
    max_acceleration: 0
  enabot_joint_4_r:
    has_position_limits: true
    min_position: -5.06145483078
    max_position:  5.06145483078
    has_velocity_limits: true
    max_velocity: 6.98131700798 
    has_acceleration_limits: false
    max_acceleration: 0
  enabot_joint_5_r:
    has_position_limits: true
    min_position: -1.53588974176
    max_position:  2.40855436775
    has_velocity_limits: true
    max_velocity: 6.98131700798 
    has_acceleration_limits: false
    max_acceleration: 0
  enabot_joint_6_r:
    has_position_limits: true
    min_position: -3.99680398707
    max_position:  3.99680398707
    has_velocity_limits: true
    max_velocity: 6.98131700798 
    has_acceleration_limits: false
    max_acceleration: 0
  enabot_joint_7_r:
    has_position_limits: true
    min_position: -2.94087978961
    max_position:  2.94087978961
    has_velocity_limits: true
    max_velocity: 3.14159265359 
    has_acceleration_limits: false
    max_acceleration: 0

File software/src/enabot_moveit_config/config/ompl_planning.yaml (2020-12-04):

planner_configs:
  SBLkConfigDefault:
    type: geometric::SBL
    range: 0.0  # Max motion added to tree. ==> maxDistance_ default: 0.0, if 0.0, set on setup()
  ESTkConfigDefault:
    type: geometric::EST
    range: 0.0  # Max motion added to tree. ==> maxDistance_ default: 0.0, if 0.0 setup()
    goal_bias: 0.05  # When close to goal select goal, with this probability. default: 0.05
  LBKPIECEkConfigDefault:
    type: geometric::LBKPIECE
    range: 0.0  # Max motion added to tree. ==> maxDistance_ default: 0.0, if 0.0, set on setup()
    border_fraction: 0.9  # Fraction of time focused on boarder default: 0.9
    min_valid_path_fraction: 0.5  # Accept partially valid moves above fraction. default: 0.5
  BKPIECEkConfigDefault:
    type: geometric::BKPIECE
    range: 0.0  # Max motion added to tree. ==> maxDistance_ default: 0.0, if 0.0, set on setup()
    border_fraction: 0.9  # Fraction of time focused on boarder default: 0.9
    failed_expansion_score_factor: 0.5  # When extending motion fails, scale score by factor. default: 0.5
    min_valid_path_fraction: 0.5  # Accept partially valid moves above fraction. default: 0.5
  KPIECEkConfigDefault:
    type: geometric::KPIECE
    range: 0.0  # Max motion added to tree. ==> maxDistance_ default: 0.0, if 0.0, set on setup()
    goal_bias: 0.05  # When close to goal select goal, with this probability. default: 0.05 
    border_fraction: 0.9  # Fraction of time focused on boarder default: 0.9 (0.0,1.]
    failed_expansion_score_factor: 0.5  # When extending motion fails, scale score by factor. default: 0.5
    min_valid_path_fraction: 0.5  # Accept partially valid moves above fraction. default: 0.5
  RRTkConfigDefault:
    type: geometric::RRT
    range: 0.0  # Max motion added to tree. ==> maxDistance_ default: 0.0, if 0.0, set on setup()
    goal_bias: 0.05  # When close to goal select goal, with this probability? default: 0.05
  RRTConnectkConfigDefault:
    type: geometric::RRTConnect
    range: 0.0  # Max motion added to tree. ==> maxDistance_ default: 0.0, if 0.0, set on setup()
  RRTstarkConfigDefault:
    type: geometric::RRTstar
    range: 0.0  # Max motion added to tree. ==> maxDistance_ default: 0.0, if 0.0, set on setup()
    goal_bias: 0.05  # When close to goal select goal, with this probability? default: 0.05
    delay_collision_checking: 1  # Stop collision checking as soon as C-free parent found. default 1
  TRRTkConfigDefault:
    type: geometric::TRRT
    range: 0.0  # Max motion added to tree. ==> maxDistance_ default: 0.0, if 0.0, set on setup()
    goal_bias: 0.05  # When close to goal select goal, with this probability? default: 0.05
    max_states_failed: 10  # when to start increasing temp. default: 10
    temp_change_factor: 2.0  # how much to increase or decrease temp. default: 2.0
    min_temperature: 10e-10  # lower limit of temp change. default: 10e-10
    init_temperature: 10e-6  # initial temperature. default: 10e-6
    frountier_threshold: 0.0  # dist new state to nearest neighbor to disqualify as frontier. default: 0.0 set in setup() 
    frountierNodeRatio: 0.1  # 1/10, or 1 nonfrontier for every 10 frontier. default: 0.1
    k_constant: 0.0  # value used to normalize expresssion. default: 0.0 set in setup()
  PRMkConfigDefault:
    type: geometric::PRM
    max_nearest_neighbors: 10  # use k nearest neighbors. default: 10
  PRMstarkConfigDefault:
    type: geometric::PRMstar
rarm:
  planner_configs:
    - SBLkConfigDefault
    - ESTkConfigDefault
    - LBKPIECEkConfigDefault
    - BKPIECEkConfigDefault
    - KPIECEkConfigDefault
    - RRTkConfigDefault
    - RRTConnectkConfigDefault
    - RRTstarkConfigDefault
    - TRRTkConfigDefault
    - PRMkConfigDefault
    - PRMstarkConfigDefault

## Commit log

2020-12-04 initial version
    [AR连线图.xlsx, AS连线图.xlsx, B308-A.SLDPRT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]
2020-12-11 all some tech doc.
    [connector.xlsx]
2020-12-11 add some motor tech docs.
2020-12-27 modify some small mechanical parts.
    [主轴垫片-0.5mm.STL, 机械制动1-a.STL, 机械制动1-b.STL]
2021-01-14 correct some moveit config errors.
    [controllers.yaml, enabot.urdf.xacro, enabot.urdf1.xacro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]
2021-01-20 initialize the Delta and CurPos value.
    [connector.xlsx]
2021-01-27 correct a bug of l1r cable rack.
    [l1r.SLDASM, l1r主壳.sldprt, l1r主轴.sldprt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]
2021-05-08 l5r fitted for 'ltd-05no' photoelectric limit sensor.
    [l1r.SLDASM, l2r.SLDASM, l3r.SLDASM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]
2022-07-08 l5r link length 109.15mm to 109mm
    [base_b.SLDPRT, l5r.SLDASM, l5r主轴.sldprt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]
2022-07-09 add a new base for single manipulator
    [base_b.SLDASM, base_b.SLDPRT, base_b基座.SLDPRT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]
2022-07-09 clear some tiny interference
    [B308-A.SLDPRT, base_b.SLDASM, l1r.SLDASM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]
2022-07-09 correct B308-A 3d-model for VEXTA ASM46AA2-Hxxx
    [B308-A.SLDPRT, base_b.SLDASM, l1r.SLDASM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]
2022-07-19 change base_b color
    [base_b.SLDASM, base_b.SLDPRT, base_b基座.SLDPRT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]
2022-07-24 rename base link
    [base.SLDPRT, base_b.SLDASM, base_b.SLDPRT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]
2022-10-09 add simulation model with urdf exporter
    [l1r.SLDPRT, l5r.SLDPRT, l7r.SLDPRT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]
2022-10-09 optimized l6r curved surface
    [l1r.SLDASM, l1r主壳.sldprt, l1r主轴.sldprt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]
2023-04-18 matlab models opened
    [base_link.STL, enabot_v5.urdf, l1r.STL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]
